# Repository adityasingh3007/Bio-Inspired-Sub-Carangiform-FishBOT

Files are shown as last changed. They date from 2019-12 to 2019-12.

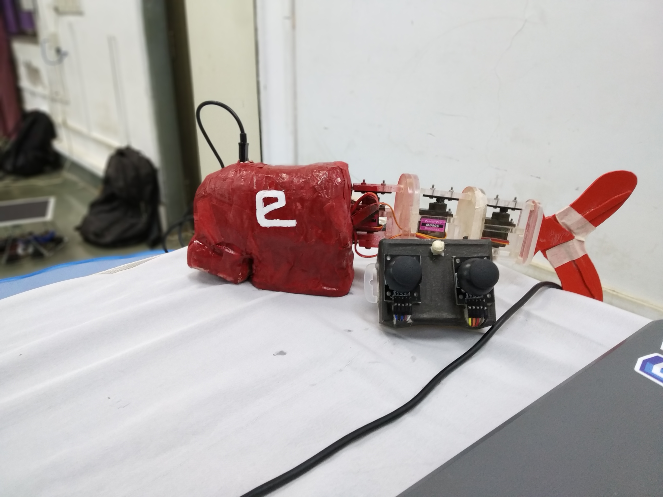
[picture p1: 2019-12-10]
Images/Final_setup.jpg

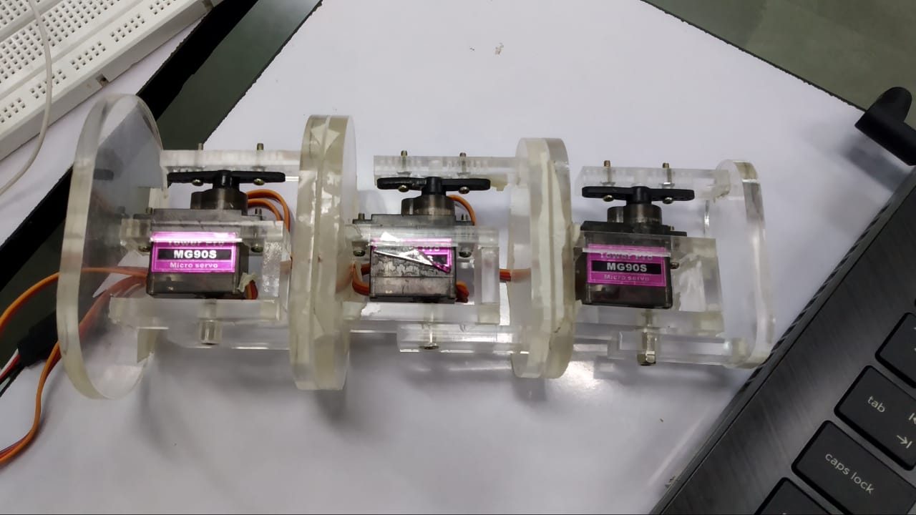
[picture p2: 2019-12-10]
Miscellaneous Files/Extra Images/Assembly_1.jpeg

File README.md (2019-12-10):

# Bio-inspired-sub-carangiform-fishbot-2019

# Abstract:

Researches about underwater propulsion mainly illustrate the use of propellers or thrusters to propel a robot in an underwater environment whereas most of the aquatic animals change their body shape in order to navigate.The shape-change generating propulsion force makes them move forward or backward effectively.The underwater fish robot is a kind of bionic robot which changes its body shape to navigate in underwater environment.The aim of the project is to understand the dynamics of underwater robots in general and the effect of lift, drag and hydrodynamic coefficients on them and to simulate, validate and develop a fish bot robot which is robust enough to carry out underwater exploratory tasks.

## Team:

  • Aditya Kumar Singh [https://github.com/adityasingh3007]

  • Bhavy Shah [https://github.com/Ragnhide]

## Mentors:

  • Rucmenya Bessariya 

  • Saail Narvekar 

  • Lohit Penubaku 

# Repository Organized.

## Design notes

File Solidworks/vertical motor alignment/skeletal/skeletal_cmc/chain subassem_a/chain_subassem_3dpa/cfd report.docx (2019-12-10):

FULL REPORT

System Info

Product | Flow Simulation 2019 SP1.0. Build: 4429
Computer name | DESKTOP-UHNF5GV
User name | Bhavy
Processors | Intel(R) Core(TM) i5-7200U CPU @ 2.50GHz
Memory | 8060 MB / 134217727 MB
Operating system | Windows 10 (or higher) (Version 10.0.17134)
CAD version | SOLIDWORKS 2019 SP1.0
CPU speed | 2701 MHz

General Info

Model | chain assembly_a_3.SLDASM
Project name | Project(1)
Project path | D:\eYSIP\Fishbot\model\F_1\vertical motor alignment\skeletal\skeletal_cmc\chain subassem_a\chain_subassem_3dpa\2
Units system | SI (m-kg-s)
Analysis type | External (not exclude internal spaces)
Exclude cavities without flow conditions | Off
Coordinate system | Global coordinate system
Reference axis | X

INPUT DATA

Global Mesh Settings

Automatic initial mesh: On

Result resolution level: 3

Advanced narrow channel refinement: Off

Refinement in solid region: Off

Geometry Resolution

Evaluation of minimum gap size: Automatic

Evaluation of minimum wall thickness: Automatic

Computational Domain

Size

X min | -0.344 m
X max | 0.482 m
Y min | -0.209 m
Y max | 0.301 m
Z min | -0.189 m
Z max | 0.299 m
X size | 0.826 m
Y size | 0.509 m
Z size | 0.488 m

Boundary Conditions

2D plane flow | None
At X min | Default
At X max | Default
At Y min | Default
At Y max | Default
At Z min | Default
At Z max | Default

Physical Features

Heat conduction in solids: Off

Time dependent: On

Gravitational effects: On

Rotation: Off

Flow type: Laminar only

Cavitation: Off

High Mach number flow: Off

Free surface: Off

Default roughness: 0 micrometer

Gravitational Settings

X component | 0 m/s^2
Y component | -9.81 m/s^2
Z component | 0 m/s^2

Default wall conditions: Adiabatic wall

Ambient Conditions

Thermodynamic parameters | Static Pressure: 5930.00 Pa Temperature: 293.20 K
Velocity parameters | Velocity vector Velocity in X direction: 0.300 m/s Velocity in Y direction: 0 m/s Velocity in Z direction: 0 m/s

Material Settings

Fluids

Water

Fluid Subdomains

Fluid Subdomain 1

Fluids | Water

Faces

Face<20>@ch_t_u-3 Face<3>@ch_t_u-3 Face<165>@9g servo_cmc-3 Face<163>@9g servo_cmc-3 Face<158>@9g servo_cmc-3 Face<148>@9g servo_cmc-3 Face<121>@dual header_cmc-3 Face<110>@dual header_cmc-3 Face<298>@ch_head-1 Face<57>@ch_h_u-3 Face<48>@ch_h_u-3 Face<48>@ch_h_u-2 Face<263>@chain tail_j2_cmc_a-1 Face<261>@chain tail_j2_cmc_a-1 Face<251>@chain tail_j2_cmc_a-1 Face<234>@chain head_j2_cmc_a-1 Face<178>@ch_h_m-2 Face<174>@ch_h_m-2 Face<170>@ch_h_m-2 Face<168>@ch_h_m-2 Face<129>@dual header_cmc-2 Face<128>@dual header_cmc-2 Face<115>@dual header_cmc-2 Face<112>@dual header_cmc-2 Face<109>@dual header_cmc-2 Face<212>@chain tail_cmc_a-1 Face<193>@ch_h_l-2 Face<191>@ch_h_l-2 Face<13>@ch_t_u-1 Face<161>@9g servo_cmc-1 Face<154>@9g servo_cmc-1 Face<112>@dual header_cmc-1 Face<90>@chain head_cmc_a-1 Face<72>@chain tail_j1_cmc_a-1 Face<57>@ch_h_u-1 Face<43>@chain head_j1_cmc_a-1 Face<38>@chain head_j1_cmc_a-1 Face<20>@ch_t_u-2 Face<19>@ch_t_u-2 Face<9>@ch_t_u-2 Face<8>@ch_t_u-2 Face<8>@ch_t_u-3 Face<4>@ch_t_u-3 Face<135>@9g servo_cmc-3 Face<128>@dual header_cmc-3 Face<125>@dual header_cmc-3 Face<124>@dual header_cmc-3 Face<365>@nose_3dpa-1 Face<350>@nose_3dpa-1 Face<337>@nose_3dpa-1 Face<318>@skin_3dpa-1 Face<294>@ch_head-1 Face<274>@ch_head-1 Face<273>@ch_head-1 Face<52>@ch_h_u-2 Face<50>@ch_h_u-2 Face<256>@chain tail_j2_cmc_a-1 Face<222>@chain head_j2_cmc_a-1 Face<218>@chain head_j2_cmc_a-1 Face<133>@dual header_cmc-2 Face<130>@dual header_cmc-2 Face<116>@dual header_cmc-2 Face<200>@chain tail_cmc_a-1 Face<179>@ch_h_m-1 Face<3>@ch_t_u-1 Face<1>@ch_t_u-1 Face<164>@9g servo_cmc-1 Face<89>@chain head_cmc_a-1 Face<78>@chain tail_j1_cmc_a-1 Face<51>@ch_h_u-1 Face<41>@chain head_j1_cmc_a-1 Face<10>@ch_t_u-3 Face<146>@9g servo_cmc-3 Face<235>@ch_t_l-4 Face<336>@nose_3dpa-1 Face<314>@MPU6050-1 Face<302>@lipo_charger_ckt-3 Face<280>@ch_head-1 Face<49>@ch_h_u-3 Face<56>@ch_h_u-2 Face<241>@ch_t_l-2 Face<145>@9g servo_cmc-2 Face<171>@ch_h_m-2 Face<119>@dual header_cmc-2 Face<192>@ch_h_l-3 Face<189>@ch_h_l-3 Face<183>@ch_h_l-3 Face<189>@ch_h_l-1 Face<141>@9g servo_cmc-1 Face<93>@chain head_cmc_a-1 Face<35>@chain head_j1_cmc_a-1 Face<18>@ch_t_u-2 Face<17>@ch_t_u-2 Face<15>@ch_t_u-3 Face<13>@ch_t_u-3 Face<155>@9g servo_cmc-3 Face<149>@9g servo_cmc-3 Face<244>@ch_t_l-3 Face<237>@ch_t_l-3 Face<342>@nose_3dpa-1 Face<330>@skin_3dpa-1 Face<327>@skin_3dpa-1 Face<308>@MPU6050-1 Face<61>@ch_h_u-3 Face<52>@ch_h_u-3 Face<47>@ch_h_u-2 Face<45>@ch_h_u-2 Face<150>@9g servo_cmc-2 Face<127>@dual header_cmc-2 Face<126>@dual header_cmc-2 Face<113>@dual header_cmc-2 Face<211>@chain tail_cmc_a-1 Face<193>@ch_h_l-3 Face<186>@ch_h_l-3 Face<172>@ch_h_m-1 Face<16>@ch_t_u-1 Face<167>@9g servo_cmc-1 Face<150>@9g servo_cmc-1 Face<138>@9g servo_cmc-1 Face<133>@dual header_cmc-1 Face<119>@dual header_cmc-1 Face<100>@chain head_cmc_a-1 Face<98>@chain head_cmc_a-1 Face<77>@chain tail_j1_cmc_a-1 Face<45>@ch_h_u-1 Face<37>@chain head_j1_cmc_a-1 Face<29>@chain head_j1_cmc_a-1 Face<23>@chain head_j1_cmc_a-1 Face<15>@ch_t_u-2 Face<14>@ch_t_u-2 Face<5>@ch_t_u-2 Face<242>@ch_t_l-4 Face<129>@dual header_cmc-3 Face<126>@dual header_cmc-3 Face<333>@skin_3dpa-1 Face<320>@skin_3dpa-1 Face<319>@skin_3dpa-1 Face<269>@lipo-1 Face<279>@ch_head-1 Face<278>@ch_head-1 Face<275>@ch_head-1 Face<270>@lipo-2 Face<54>@ch_h_u-3 Face<50>@ch_h_u-3 Face<57>@ch_h_u-2 Face<265>@chain tail_j2_cmc_a-1 Face<257>@chain tail_j2_cmc_a-1 Face<164>@9g servo_cmc-2 Face<153>@9g servo_cmc-2 Face<151>@9g servo_cmc-2 Face<144>@9g servo_cmc-2 Face<221>@chain head_j2_cmc_a-1 Face<181>@ch_h_m-3 Face<125>@dual header_cmc-2 Face<120>@dual header_cmc-2 Face<197>@chain tail_cmc_a-1 Face<186>@ch_h_l-2 Face<187>@ch_h_l-1 Face<170>@ch_h_m-1 Face<169>@ch_h_m-1 Face<20>@ch_t_u-1 Face<166>@9g servo_cmc-1 Face<146>@9g servo_cmc-1 Face<121>@dual header_cmc-1 Face<81>@chain tail_j1_cmc_a-1 Face<79>@chain tail_j1_cmc_a-1 Face<71>@chain tail_j1_cmc_a-1 Face<47>@ch_h_u-1 Face<22>@ch_t_u-3 Face<7>@ch_t_u-3 Face<161>@9g servo_cmc-3 Face<153>@9g servo_cmc-3 Face<140>@9g servo_cmc-3 Face<241>@ch_t_l-3 Face<239>@ch_t_l-4 Face<369>@buck_cnvrtr-1 Face<368>@buck_cnvrtr-1 Face<118>@dual header_cmc-3 Face<107>@dual header_cmc-3 Face<358>@nose_3dpa-1 Face<353>@nose_3dpa-1 Face<352>@nose_3dpa-1 Face<351>@nose_3dpa-1 Face<297>@ch_head-1 Face<60>@ch_h_u-3 Face<253>@chain tail_j2_cmc_a-1 Face<250>@chain tail_j2_cmc_a-1 Face<248>@chain tail_j2_cmc_a-1 Face<246>@chain tail_j2_cmc_a-1 Face<242>@ch_t_l-2 Face<238>@ch_t_l-2 Face<160>@9g servo_cmc-2 Face<138>@9g servo_cmc-2 Face<178>@ch_h_m-3 Face<180>@ch_h_m-2 Face<131>@dual header_cmc-2 Face<121>@dual header_cmc-2 Face<110>@dual header_cmc-2 Face<191>@ch_h_l-3 Face<196>@ch_h_l-2 Face<177>@ch_h_m-1 Face<174>@ch_h_m-1 Face<9>@ch_t_u-1 Face<8>@ch_t_u-1 Face<159>@9g servo_cmc-1 Face<156>@9g servo_cmc-1 Face<151>@9g servo_cmc-1 Face<124>@dual header_cmc-1 Face<114>@dual header_cmc-1 Face<94>@chain head_cmc_a-1 Face<91>@chain head_cmc_a-1 Face<86>@chain head_cmc_a-1 Face<49>@ch_h_u-1 Face<42>@chain head_j1_cmc_a-1 Face<36>@chain head_j1_cmc_a-1 Face<6>@ch_t_u-2 Face<4>@ch_t_u-2 Face<150>@9g servo_cmc-3 Face<143>@9g servo_cmc-3 Face<139>@9g servo_cmc-3 Face<243>@ch_t_l-4 Face<112>@dual header_cmc-3 Face<109>@dual header_cmc-3 Face<360>@nose_3dpa-1 Face<355>@nose_3dpa-1 Face<349>@nose_3dpa-1 Face<311>@MPU6050-1 Face<284>@ch_head-1 Face<282>@ch_head-1 Face<63>@ch_h_u-3 Face<58>@ch_h_u-3 Face<51>@ch_h_u-3 Face<51>@ch_h_u-2 Face<49>@ch_h_u-2 Face<258>@chain tail_j2_cmc_a-1 Face<154>@9g servo_cmc-2 Face<229>@chain head_j2_cmc_a-1 Face<177>@ch_h_m-3 Face<173>@ch_h_m-3 Face<170>@ch_h_m-3 Face<177>@ch_h_m-2 Face<123>@dual header_cmc-2 Face<107>@dual header_cmc-2 Face<192>@ch_h_l-2 Face<188>@ch_h_l-2 Face<191>@ch_h_l-1 Face<185>@ch_h_l-1 Face<184>@ch_h_l-1 Face<19>@ch_t_u-1 Face<165>@9g servo_cmc-1 Face<118>@dual header_cmc-1 Face<109>@dual header_cmc-1 Face<83>@chain tail_j1_cmc_a-1 Face<74>@chain tail_j1_cmc_a-1 Face<67>@chain tail_j1_cmc_a-1 Face<58>@ch_h_u-1 Face<16>@ch_t_u-3 Face<1>@ch_t_u-3 Face<157>@9g servo_cmc-3 Face<243>@ch_t_l-3 Face<244>@ch_t_l-4 Face<133>@dual header_cmc-3 Face<132>@dual header_cmc-3 Face<122>@dual header_cmc-3 Face<120>@dual header_cmc-3 Face<359>@nose_3dpa-1 Face<356>@nose_3dpa-1 Face<343>@nose_3dpa-1 Face<270>@lipo-1 Face<309>@MPU6050-1 Face<296>@ch_head-1 Face<290>@ch_head-1 Face<283>@ch_head-1 Face<272>@lipo-2 Face<62>@ch_h_u-2 Face<54>@ch_h_u-2 Face<156>@9g servo_cmc-2 Face<141>@9g servo_cmc-2 Face<135>@9g servo_cmc-2 Face<215>@chain head_j2_cmc_a-1 Face<180>@ch_h_m-3 Face<174>@ch_h_m-3 Face<114>@dual header_cmc-2 Face<195>@ch_h_l-3 Face<187>@ch_h_l-2 Face<182>@ch_h_l-2 Face<186>@ch_h_l-1 Face<176>@ch_h_m-1 Face<12>@ch_t_u-1 Face<7>@ch_t_u-1 Face<129>@dual header_cmc-1 Face<127>@dual header_cmc-1 Face<123>@dual header_cmc-1 Face<116>@dual header_cmc-1 Face<97>@chain head_cmc_a-1 Face<87>@chain head_cmc_a-1 Face<31>@chain head_j1_cmc_a-1 Face<6>@ch_t_u-3 Face<138>@9g servo_cmc-3 Face<137>@9g servo_cmc-3 Face<134>@9g servo_cmc-3 Face<240>@ch_t_l-4 Face<236>@ch_t_l-4 Face<370>@buck_cnvrtr-1 Face<366>@buck_cnvrtr-1 Face<127>@dual header_cmc-3 Face<115>@dual header_cmc-3 Face<106>@dual header_cmc-3 Face<340>@nose_3dpa-1 Face<312>@MPU6050-1 Face<306>@MPU6050-1 Face<292>@ch_head-1 Face<53>@ch_h_u-3 Face<63>@ch_h_u-2 Face<59>@ch_h_u-2 Face<252>@chain tail_j2_cmc_a-1 Face<235>@ch_t_l-2 Face<166>@9g servo_cmc-2 Face<157>@9g servo_cmc-2 Face<149>@9g servo_cmc-2 Face<142>@9g servo_cmc-2 Face<217>@chain head_j2_cmc_a-1 Face<171>@ch_h_m-3 Face<175>@ch_h_m-2 Face<122>@dual header_cmc-2 Face<108>@dual header_cmc-2 Face<210>@chain tail_cmc_a-1 Face<199>@chain tail_cmc_a-1 Face<189>@ch_h_l-2 Face<184>@ch_h_l-2 Face<192>@ch_h_l-1 Face<22>@ch_t_u-1 Face<14>@ch_t_u-1 Face<149>@9g servo_cmc-1 Face<143>@9g servo_cmc-1 Face<99>@chain head_cmc_a-1 Face<96>@chain head_cmc_a-1 Face<46>@ch_h_u-1 Face<34>@chain head_j1_cmc_a-1 Face<33>@chain head_j1_cmc_a-1 Face<25>@chain head_j1_cmc_a-1 Face<24>@chain head_j1_cmc_a-1 Face<1>@ch_t_u-2 Face<18>@ch_t_u-3 Face<238>@ch_t_l-4 Face<111>@dual header_cmc-3 Face<332>@skin_3dpa-1 Face<328>@skin_3dpa-1 Face<325>@skin_3dpa-1 Face<315>@skin_3dpa-1 Face<268>@lipo-1 Face<310>@MPU6050-1 Face<277>@ch_head-1 Face<47>@ch_h_u-3 Face<55>@ch_h_u-2 Face<243>@ch_t_l-2 Face<236>@ch_t_l-2 Face<167>@9g servo_cmc-2 Face<136>@9g servo_cmc-2 Face<134>@9g servo_cmc-2 Face<233>@chain head_j2_cmc_a-1 Face<172>@ch_h_m-2 Face<207>@chain tail_cmc_a-1 Face<184>@ch_h_l-3 Face<182>@ch_h_l-3 Face<196>@ch_h_l-1 Face<182>@ch_h_l-1 Face<171>@ch_h_m-1 Face<21>@ch_t_u-1 Face<160>@9g servo_cmc-1 Face<92>@chain head_cmc_a-1 Face<70>@chain tail_j1_cmc_a-1 Face<62>@ch_h_u-1 Face<52>@ch_h_u-1 Face<26>@chain head_j1_cmc_a-1 Face<22>@ch_t_u-2 Face<21>@ch_t_u-2 Face<13>@ch_t_u-2 Face<2>@ch_t_u-3 Face<162>@9g servo_cmc-3 Face<159>@9g servo_cmc-3 Face<144>@9g servo_cmc-3 Face<245>@ch_t_l-3 Face<241>@ch_t_l-4 Face<364>@nose_3dpa-1 Face<354>@nose_3dpa-1 Face<344>@nose_3dpa-1 Face<329>@skin_3dpa-1 Face<326>@skin_3dpa-1 Face<272>@lipo-1 Face<271>@lipo-1 Face<305>@MPU6050-1 Face<56>@ch_h_u-3 Face<58>@ch_h_u-2 Face<262>@chain tail_j2_cmc_a-1 Face<259>@chain tail_j2_cmc_a-1 Face<254>@chain tail_j2_cmc_a-1 Face<240>@ch_t_l-2 Face<223>@chain head_j2_cmc_a-1 Face<111>@dual header_cmc-2 Face<194>@ch_h_l-2 Face<185>@ch_h_l-2 Face<195>@ch_h_l-1 Face<188>@ch_h_l-1 Face<183>@ch_h_l-1 Face<175>@ch_h_m-1 Face<15>@ch_t_u-1 Face<153>@9g servo_cmc-1 Face<148>@9g servo_cmc-1 Face<147>@9g servo_cmc-1 Face<144>@9g servo_cmc-1 Face<139>@9g servo_cmc-1 Face<130>@dual header_cmc-1 Face<125>@dual header_cmc-1 Face<88>@chain head_cmc_a-1 Face<40>@chain head_j1_cmc_a-1 Face<12>@ch_t_u-2 Face<11>@ch_t_u-2 Face<160>@9g servo_cmc-3 Face<141>@9g servo_cmc-3 Face<239>@ch_t_l-3 Face<245>@ch_t_l-4 Face<362>@nose_3dpa-1 Face<335>@nose_3dpa-1 Face<291>@ch_head-1 Face<287>@ch_head-1 Face<286>@ch_head-1 Face<271>@lipo-2 Face<268>@lipo-2 Face<45>@ch_h_u-3 Face<53>@ch_h_u-2 Face<158>@9g servo_cmc-2 Face<155>@9g servo_cmc-2 Face<152>@9g servo_cmc-2 Face<231>@chain head_j2_cmc_a-1 Face<225>@chain head_j2_cmc_a-1 Face<224>@chain head_j2_cmc_a-1 Face<220>@chain head_j2_cmc_a-1 Face<169>@ch_h_m-3 Face<173>@ch_h_m-2 Face<132>@dual header_cmc-2 Face<213>@chain tail_cmc_a-1 Face<205>@chain tail_cmc_a-1 Face<195>@ch_h_l-2 Face<183>@ch_h_l-2 Face<194>@ch_h_l-1 Face<178>@ch_h_m-1 Face<4>@ch_t_u-1 Face<155>@9g servo_cmc-1 Face<122>@dual header_cmc-1 Face<113>@dual header_cmc-1 Face<101>@chain head_cmc_a-1 Face<65>@chain tail_j1_cmc_a-1 Face<27>@chain head_j1_cmc_a-1 Face<10>@ch_t_u-2 Face<7>@ch_t_u-2 Face<21>@ch_t_u-3 Face<167>@9g servo_cmc-3 Face<166>@9g servo_cmc-3 Face<156>@9g servo_cmc-3 Face<152>@9g servo_cmc-3 Face<113>@dual header_cmc-3 Face<361>@nose_3dpa-1 Face<345>@nose_3dpa-1 Face<322>@skin_3dpa-1 Face<317>@skin_3dpa-1 Face<313>@MPU6050-1 Face<303>@lipo_charger_ckt-3 Face<301>@lipo_charger_ckt-3 Face<300>@lipo_charger_ckt-3 Face<299>@lipo_charger_ckt-3 Face<295>@ch_head-1 Face<288>@ch_head-1 Face<281>@ch_head-1 Face<276>@ch_head-1 Face<55>@ch_h_u-3 Face<44>@ch_h_u-3 Face<61>@ch_h_u-2 Face<44>@ch_h_u-2 Face<264>@chain tail_j2_cmc_a-1 Face<162>@9g servo_cmc-2 Face<147>@9g servo_cmc-2 Face<140>@9g servo_cmc-2 Face<228>@chain head_j2_cmc_a-1 Face<169>@ch_h_m-2 Face<204>@chain tail_cmc_a-1 Face<203>@chain tail_cmc_a-1 Face<198>@chain tail_cmc_a-1 Face<194>@ch_h_l-3 Face<190>@ch_h_l-3 Face<18>@ch_t_u-1 Face<10>@ch_t_u-1 Face<2>@ch_t_u-1 Face<158>@9g servo_cmc-1 Face<152>@9g servo_cmc-1 Face<140>@9g servo_cmc-1 Face<135>@9g servo_cmc-1 Face<120>@dual header_cmc-1 Face<115>@dual header_cmc-1 Face<111>@dual header_cmc-1 Face<107>@dual header_cmc-1 Face<80>@chain tail_j1_cmc_a-1 Face<73>@chain tail_j1_cmc_a-1 Face<68>@chain tail_j1_cmc_a-1 Face<60>@ch_h_u-1 Face<59>@ch_h_u-1 Face<39>@chain head_j1_cmc_a-1 Face<16>@ch_t_u-2 Face<3>@ch_t_u-2 Face<14>@ch_t_u-3 Face<5>@ch_t_u-3 Face<147>@9g servo_cmc-3 Face<145>@9g servo_cmc-3 Face<242>@ch_t_l-3 Face<237>@ch_t_l-4 Face<131>@dual header_cmc-3 Face<119>@dual header_cmc-3 Face<117>@dual header_cmc-3 Face<116>@dual header_cmc-3 Face<346>@nose_3dpa-1 Face<341>@nose_3dpa-1 Face<339>@nose_3dpa-1 Face<334>@nose_3dpa-1 Face<324>@skin_3dpa-1 Face<316>@skin_3dpa-1 Face<293>@ch_head-1 Face<285>@ch_head-1 Face<267>@lipo-2 Face<46>@ch_h_u-3 Face<46>@ch_h_u-2 Face<161>@9g servo_cmc-2 Face<146>@9g servo_cmc-2 Face<143>@9g servo_cmc-2 Face<139>@9g servo_cmc-2 Face<230>@chain head_j2_cmc_a-1 Face<226>@chain head_j2_cmc_a-1 Face<117>@dual header_cmc-2 Face<106>@dual header_cmc-2 Face<209>@chain tail_cmc_a-1 Face<185>@ch_h_l-3 Face<190>@ch_h_l-2 Face<193>@ch_h_l-1 Face<190>@ch_h_l-1 Face<137>@9g servo_cmc-1 Face<136>@9g servo_cmc-1 Face<131>@dual header_cmc-1 Face<105>@chain head_cmc_a-1 Face<104>@chain head_cmc_a-1 Face<103>@chain head_cmc_a-1 Face<84>@chain tail_j1_cmc_a-1 Face<61>@ch_h_u-1 Face<50>@ch_h_u-1 Face<28>@chain head_j1_cmc_a-1 Face<12>@ch_t_u-3 Face<9>@ch_t_u-3 Face<142>@9g servo_cmc-3 Face<236>@ch_t_l-3 Face<235>@ch_t_l-3 Face<371>@buck_cnvrtr-1 Face<363>@nose_3dpa-1 Face<62>@ch_h_u-3 Face<266>@chain tail_j2_cmc_a-1 Face<249>@chain tail_j2_cmc_a-1 Face<237>@ch_t_l-2 Face<165>@9g servo_cmc-2 Face<159>@9g servo_cmc-2 Face<219>@chain head_j2_cmc_a-1 Face<214>@chain head_j2_cmc_a-1 Face<179>@ch_h_m-3 Face<176>@ch_h_m-3 Face<175>@ch_h_m-3 Face<168>@ch_h_m-3 Face<196>@ch_h_l-3 Face<187>@ch_h_l-3 Face<180>@ch_h_m-1 Face<168>@ch_h_m-1 Face<17>@ch_t_u-1 Face<162>@9g servo_cmc-1 Face<157>@9g servo_cmc-1 Face<134>@9g servo_cmc-1 Face<132>@dual header_cmc-1 Face<126>@dual header_cmc-1 Face<108>@dual header_cmc-1 Face<82>@chain tail_j1_cmc_a-1 Face<76>@chain tail_j1_cmc_a-1 Face<75>@chain tail_j1_cmc_a-1 Face<64>@chain tail_j1_cmc_a-1 Face<63>@ch_h_u-1 Face<30>@chain head_j1_cmc_a-1 Face<19>@ch_t_u-3 Face<164>@9g servo_cmc-3 Face<151>@9g servo_cmc-3 Face<136>@9g servo_cmc-3 Face<238>@ch_t_l-3 Face<367>@buck_cnvrtr-1 Face<108>@dual header_cmc-3 Face<347>@nose_3dpa-1 Face<338>@nose_3dpa-1 Face<323>@skin_3dpa-1 Face<267>@lipo-1 Face<307>@MPU6050-1 Face<304>@lipo_charger_ckt-3 Face<60>@ch_h_u-2 Face<255>@chain tail_j2_cmc_a-1 Face<247>@chain tail_j2_cmc_a-1 Face<245>@ch_t_l-2 Face<163>@9g servo_cmc-2 Face<148>@9g servo_cmc-2 Face<232>@chain head_j2_cmc_a-1 Face<181>@ch_h_m-2 Face<176>@ch_h_m-2 Face<118>@dual header_cmc-2 Face<206>@chain tail_cmc_a-1 Face<202>@chain tail_cmc_a-1 Face<181>@ch_h_m-1 Face<6>@ch_t_u-1 Face<5>@ch_t_u-1 Face<163>@9g servo_cmc-1 Face<102>@chain head_cmc_a-1 Face<95>@chain head_cmc_a-1 Face<56>@ch_h_u-1 Face<53>@ch_h_u-1 Face<48>@ch_h_u-1 Face<17>@ch_t_u-3 Face<11>@ch_t_u-3 Face<154>@9g servo_cmc-3 Face<240>@ch_t_l-3 Face<130>@dual header_cmc-3 Face<123>@dual header_cmc-3 Face<114>@dual header_cmc-3 Face<357>@nose_3dpa-1 Face<348>@nose_3dpa-1 Face<331>@skin_3dpa-1 Face<321>@skin_3dpa-1 Face<289>@ch_head-1 Face<269>@lipo-2 Face<59>@ch_h_u-3 Face<260>@chain tail_j2_cmc_a-1 Face<244>@ch_t_l-2 Face<239>@ch_t_l-2 Face<137>@9g servo_cmc-2 Face<227>@chain head_j2_cmc_a-1 Face<216>@chain head_j2_cmc_a-1 Face<172>@ch_h_m-3 Face<179>@ch_h_m-2 Face<124>@dual header_cmc-2 Face<208>@chain tail_cmc_a-1 Face<201>@chain tail_cmc_a-1 Face<188>@ch_h_l-3 Face<173>@ch_h_m-1 Face<11>@ch_t_u-1 Face<145>@9g servo_cmc-1 Face<142>@9g servo_cmc-1 Face<128>@dual header_cmc-1 Face<117>@dual header_cmc-1 Face<110>@dual header_cmc-1 Face<106>@dual header_cmc-1 Face<85>@chain head_cmc_a-1 Face<69>@chain tail_j1_cmc_a-1 Face<66>@chain tail_j1_cmc_a-1 Face<55>@ch_h_u-1 Face<54>@ch_h_u-1 Face<44>@ch_h_u-1 Face<32>@chain head_j1_cmc_a-1 Face<2>@ch_t_u-2
Coordinate system | Global coordinate system
Reference axis | X
Thermodynamic Parameters | Static Pressure: 5930.00 Pa Pressure potential: On Temperature: 293.20 K
Velocity Parameters | Velocity in X direction: 0.300 m/s Velocity in Y direction: 0 m/s Velocity in Z direction: 0 m/s
Flow type | Laminar Only
Cavitation | Off
Refer to the origin | Off

Boundary Conditions

Real Wall 1

Type | Real wall
Faces
Coordinate system | Global coordinate system
Reference axis | X

Goals

Global Goals

GG Minimum Static Pressure 1

Type | Global Goal
Goal type | Static Pressure
Calculate | Minimum value
Coordinate system | Global coordinate system
Use in convergence | On

GG Average Total Pressure 1

Type | Global Goal
Goal type | Total Pressure
Calculate | Average value
Coordinate system | Global coordinate system
Use in convergence | On

GG Maximum Dynamic Pressure 1

Type | Global Goal
Goal type | Dynamic Pressure
Calculate | Maximum value
Coordinate system | Global coordinate system
Use in convergence | On

GG Minimum Velocity (X) 1

Type | Global Goal
Goal type | Velocity (X)
Calculate | Minimum value
Coordinate system | Global coordinate system
Use in convergence | On

Calculation Control Options

Finish Conditions

Finish Conditions | If one is satisfied
Maximum physical time | 1.000 s

Solver Refinement

Refinement: Disabled

Results Saving

Save before refinement | On

Advanced Control Options

Flow Freezing

Flow freezing strategy | Disabled

Manual time step (Freezing): Off

Manual time step: Off

RESULTS

Document1 Page 1 of 1 18.06.2019

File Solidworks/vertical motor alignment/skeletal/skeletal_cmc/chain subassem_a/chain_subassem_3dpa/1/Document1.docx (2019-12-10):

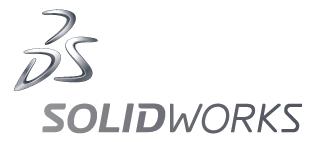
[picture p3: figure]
Description: Description: sw_vert_gray_short

[Company logo here]
[company name here] | [city, state here] | [company url here] | Fluid Flow Simulation Project Report

[name] ∙ | [title] | ∙ ∙ [email address] ∙ | (###) ###-####

# SOLIDWORKS Flow Simulation

# Project Report

March 26, 2014

[Model Picture here]

Learn more about SOLIDWORKS Flow Simulation (https://www.solidworks.com/sw/products/simulation/flow-simulation.htm)

# Table of Contents

# 1 General Information

Objective of the simulation: Lorem ipsum dolor sit amet, consectetur adipiscing elit. Ut a pulvinar lacus. Vivamus adipiscing adipiscing eleifend. Pellentesque eget ante in ante suscipit gravida in non lorem. Suspendisse hendrerit sagittis lacus non aliquam. Proin pellentesque, lorem quis consequat porta, lectus nunc vestibulum lectus, nec rhoncus libero dui ut felis. Vestibulum eu aliquet tellus. Curabitur suscipit ornare sem. Suspendisse pulvinar pharetra ultrices. Suspendisse a quam massa

## 1.1 Analysis Environment

Software Product: Flow Simulation 2019 SP1.0. Build: 4429

CPU Type: Intel(R) Core(TM) i5-7200U CPU @ 2.50GHz

CPU Speed: 2701 (400) MHz

RAM: 8060 MB / 134217727 MB

Operating System: Windows 10 (or higher) (Version 10.0.17134)

## 1.2 Model Information

Model Name: chain assembly_a_3.SLDASM

Project Name: Project(1)

## 1.3 Project Comments:

Unit System: SI (m-kg-s)

Analysis Type: External (not exclude internal spaces)

## 1.4 Size of Computational Domain

Size

X min | -0.344 m
X max | 0.482 m
Y min | -0.209 m
Y max | 0.301 m
Z min | -0.189 m
Z max | 0.299 m
X size | 0.826 m
Y size | 0.509 m
Z size | 0.488 m

## 1.5 Simulation Parameters

### 1.5.1 Mesh Settings

#### 1.5.1.1 Basic Mesh

#### 1.5.1.2 Analysis Mesh

Total Cell count:

Fluid Cells:

Solid Cells:

Partial Cells:

Trimmed Cells:

#### 1.5.1.3 Additional Physical Calculation Options

Heat Transfer Analysis: Heat conduction in solids: Off

Flow Type: Laminar only

Time-Dependent Analysis: On

Gravity: On

Radiation:

Humidity:

Default Wall Roughness: 0 micrometer

### 1.5.2 Material Settings

Material Settings

Fluids

Water

### 1.5.3 Initial Conditions

Ambient Conditions

Thermodynamic parameters | Static Pressure: 5930.00 Pa Temperature: 298.00 K
Velocity parameters | Velocity vector Velocity in X direction: 0.250 m/s Velocity in Y direction: 0 m/s Velocity in Z direction: 0 m/s

### 1.5.4 Boundary Conditions

Boundary Conditions

Real Wall 1

Type | Real wall
Faces | skin_3dpa-1/Shell1//Face skin_3dpa-1/Shell1//Face nose_3dpa-1/Sweep1//Face skin_3dpa-1/Shell1//Face skin_3dpa-1/Shell1//Face skin_3dpa-1/Shell1//Face skin_3dpa-1/Shell1//Face ch_head-1/Cut-Sweep1//Face skin_3dpa-1/Shell1//Face nose_3dpa-1/Sweep1//Face
Coordinate system | Global coordinate system
Reference axis | X

### 1.5.5 Volumetric Heat Sources

### 1.5.6 Engineering Goals

## 1.6 Analysis Time

Calculation Time: 0 s

Number of Iterations: 0

Warnings:

# 3 Results

## 3.1 Analysis Goals

## 3.2 Global Min-Max-Table

## 3.3 Results

## 3.4 Conclusion

Lorem ipsum dolor sit amet, consectetur adipiscing elit. Ut a pulvinar lacus. Vivamus adipiscing adipiscing eleifend. Pellentesque eget ante in ante suscipit gravida in non lorem. Suspendisse hendrerit sagittis lacus non aliquam. Proin pellentesque, lorem quis consequat porta, lectus nunc vestibulum lectus, nec rhoncus libero dui ut felis. Vestibulum eu aliquet tellus. Curabitur suscipit ornare sem. Suspendisse pulvinar pharetra ultrices. Suspendisse a quam massa

# 5 Appendix

## 5.1 Material Data

Engineering Database

Liquids

Water

Path: Liquids Pre-Defined

Density

Dynamic viscosity

Specific heat (Cp)

Thermal conductivity

Cavitation effect: Yes

Temperature: 0 K

Saturation pressure: 0 Pa

Radiation properties: No

Fluid Flow Simulation Report

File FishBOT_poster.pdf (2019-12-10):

# Bio-Inspired Sub-carangiform Fishbot

## Aditya Kumar Singh, Bhavy Shah, Mentor: Rucmenya, Lohit, Saail

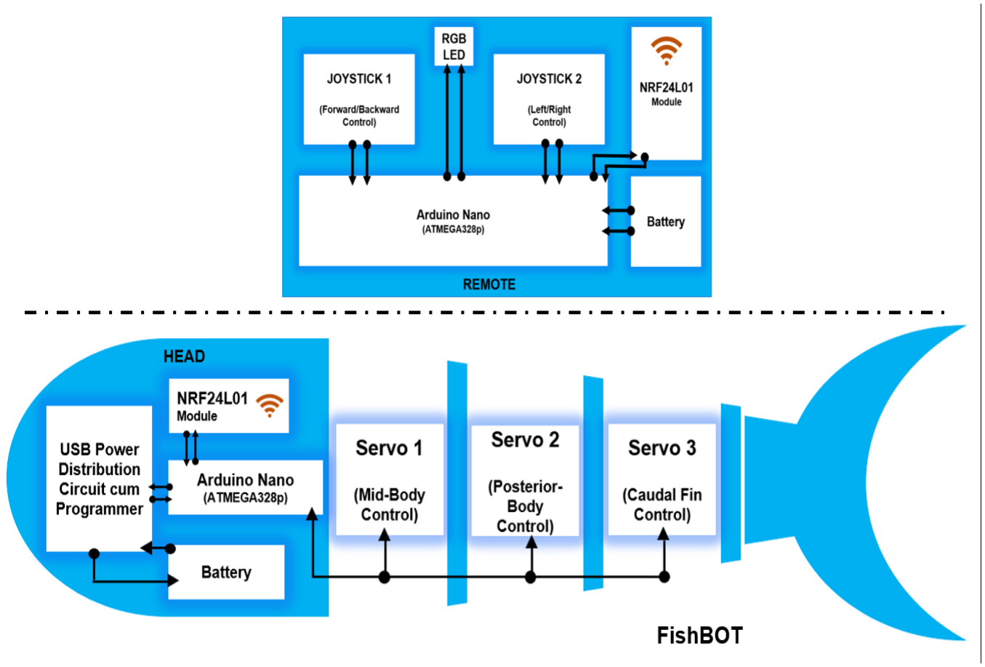
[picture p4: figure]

## e-Yantra Summer Internship Project 2019

## Abstract

Underwater robotics is a great option to carry out various underwater operations like environmental inspection, monitoring natural resources, defense operations, underwater machinery inspection and many more, remotely.

## Objective

The objective of this project is to design, develop & build a bionic subcarangiform fish that can swim and can be controlled remotely.

## Introduction

Nature has always remained an inspiration to

build and innovate robots that operates similar to

real-world beings. A fish has got typical smooth

motion when it comes to underwater navigation.

It uses undulated body motion and caudal fin to

move forward and pectoral & pelvic fins for

turning operations. This robo-fish has geometry

and body resembling to a subcarangiform fish.

Block Diagram | Solidworks CAD model

## Features

+ Imitates swimming pattern of a subcarangiform fish and has streamline design.
+ Multi-segmented body for a sinusoidal motion of the body. (Length is 36cm and Turning Radius is 18cm).
+ Manevuring of the fish is achieved using only Caudal Fin and the Body motion.
+ Wirelessly controlled using NRF24L01 module (2.4 GHz ISM Band) through SPI protocol.
+ Waterproofing of electronics using plasticizer resin.

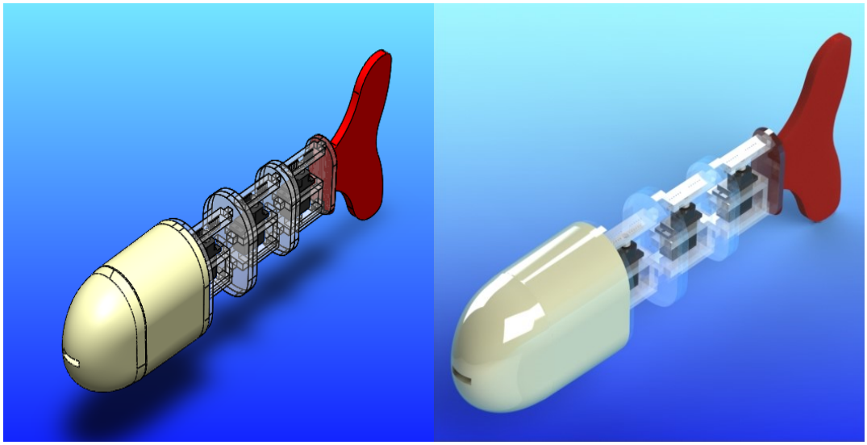
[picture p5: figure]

## Actual Model

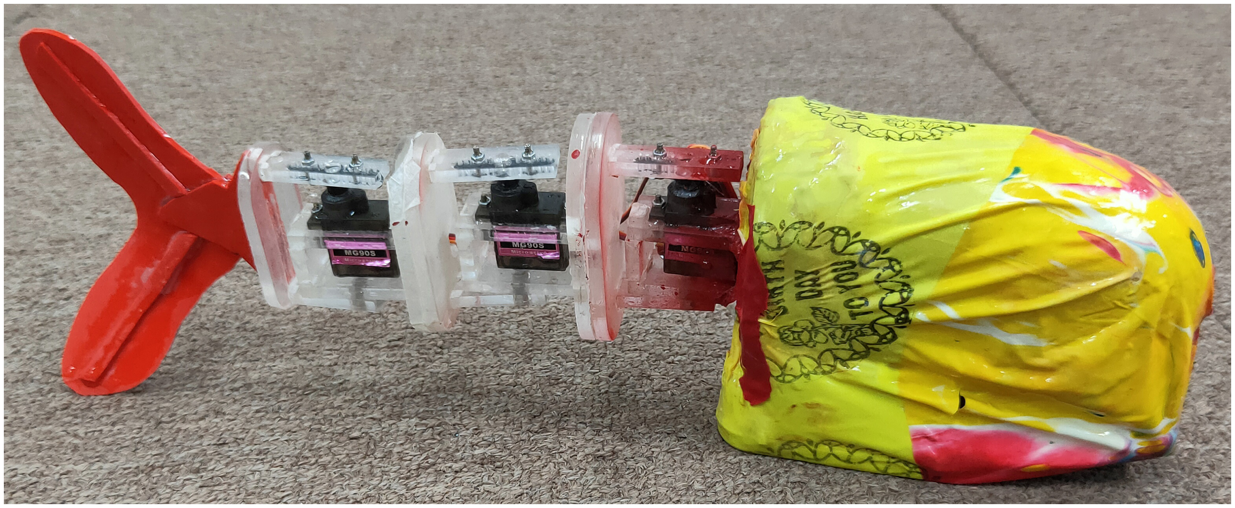
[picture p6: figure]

## Application

+ Underwater survillance.
+ Underwater exploration.
+ Robot-animal interaction.
+ Aquatic Environmental monitoring. + Education and outreach.

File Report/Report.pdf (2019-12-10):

## e-YSIP 2019

### Bio-Inspired Sub-carangiform

## FishBOT

### Intern 1: Aditya Kumar Singh Intern 2: Bhavy Shah Mentor Name: Rucmenya Bessariya Lohit Penubaku Saail Narvekar Duration of Internship: 22/05/2019 − 05/07/2019

2019, e-Yantra Publication

# Bio-Inspired Sub-carangiform Fish-BOT

## Abstract

Nature has always worked as an inspirational source for the robotics world to create & innovate things in order to understand and imitate it. This project on the same basis, is all about how to design & imitate a subcarangiform fish in respect to the nature’s creation. The FishBOT has got a 3 joint body locomotion controlled using micro servos. The caudal fin is used to generate the force vortex for each forward push and also the turns are controlled only by using lateral shift of body & caudal fin.

### Completion status

Working prototype which can swim underwater has been accomplished with great speed and efficiency as well as turning on both side can be done with effective turning radius ranging 15 to 30 cm. The length of the bot is 36 cm. Also, it is controlled using remote by NRF24L01 transceiver module. It has a battery backup of 30 minutes.

## 1.1 Hardware parts

- Arduino Nano (with Cable) (2 Pcs), Datasheet, page 1, Vendor link (https://www.amazon.in/SunRobotics-Arduino-Nano-USB-Cable/dp/B072VQL7WJ)
- NRF24L01 Module (2 Pcs), Datasheet, page 1, Vendor link (https://www.amazon.in/REES52-NRF24L01-Wireless-Transceiver-Arduino/dp/0070923507)
- Lipo Battery, 3.7 Volts (4 Pcs), Vendor link (https://www.amazon.in/Invento-battery-40x35x5mm-Quadcopter-Helicopter/dp/B07GL3VT81?s=gateway)
- Micro Servo Motor (3 Pcs), Datasheet, page 1, Vendor link (https://www.amazon.in/Robodo-Electronics-Tower-Micro-Servo/dp/B00MTFFAE0)
- LM323T Voltage Regulator (1 Pc), Datasheet, page 1, Vendor link (https://www.amazon.co.uk/LM323T-terminal-positive-regulator-220-casing/dp/B0747TDDCC)

1

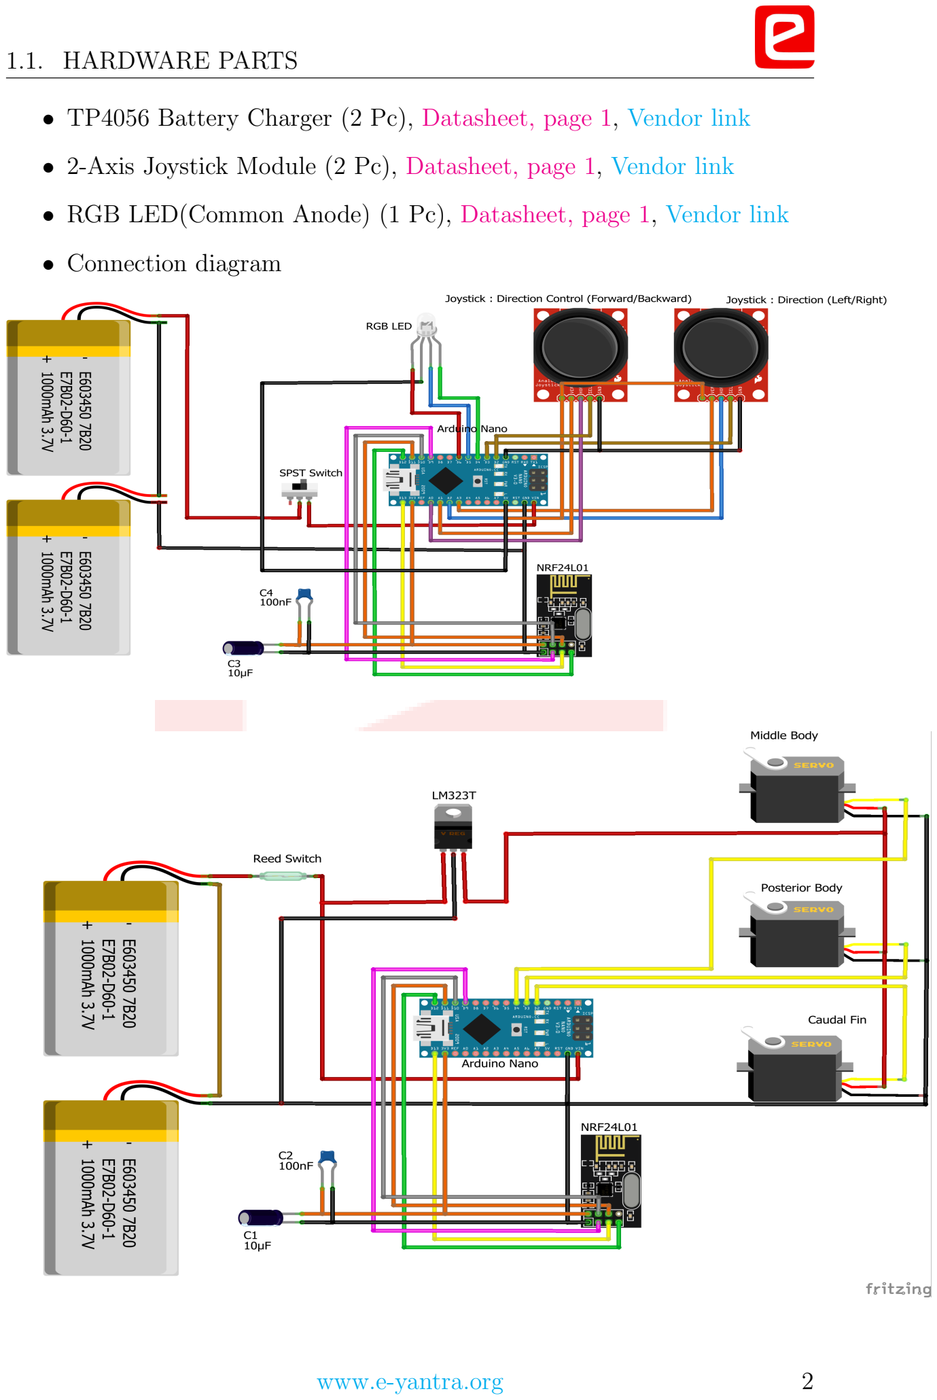
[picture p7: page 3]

1.1. HARDWARE PARTS
- TP4056 Battery Charger (2 Pc), Datasheet, page 1, Vendor link (https://robu.in/product/tp4056-1a-lipo-battery-charging-board-micro-usb-with-current-protection/)
- 2-Axis Joystick Module (2 Pc), Datasheet, page 1, Vendor link (https://www.amazon.in/Dual-Axis-Joystick-Module-Arduino-Devices/dp/B00WFDJS26)
- RGB LED(Common Anode) (1 Pc), Datasheet, page 1, Vendor link (https://www.amazon.in/Generic-PZIN14016715-Anode-Color-Diffused/dp/B01EE3NJJC?s=gateway)
- Connection diagram
www.e-yantra.org | 2

1.2. SOFTWARE USED

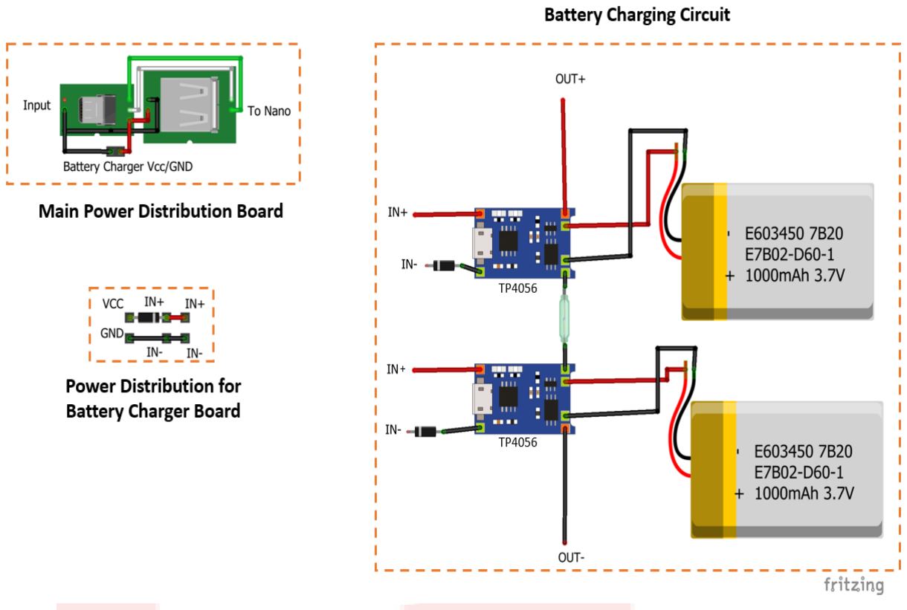
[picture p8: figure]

## 1.2 Software used

- Arduino IDE, Version:1.8.5, Link (https://www.arduino.cc/en/Main/OldSoftwareReleases)
- Solidworks Version: 2019, Link (https://my.solidworks.com/try-solidworks)
- Installation steps:

– Arduino IDE : Installation Guide (https://www.arduino.cc/en/Guide/Windows)

– Solidworks : Installation Guide (https://www.solidworks.com/sw/education/student-installation-guides-and-support.htm)

## 1.3 Assembly of Mechanical design & Electronics hardware

Getting Mechanical design model.

Get the Solidworks design of parts and assembly from this link: Link

www.e-yantra.org | 3

1.3. ASSEMBLY OF MECHANICAL DESIGN & ELECTRONICS HARDWARE

### Getting mechanical parts

Get the acrylic parts laser cut and the head & nose portion of the fish 3D printed.

### Waterproofing servo motors

- Unscrew the servos from the bottom. On the circuitry parts apply 2-3 coatings of plasticizer resin.
- On the top gear part, apply hydrophobic grease and then screw it back.
- Further, apply multiple coatings of the resin on entire servo motor body (keeping care near the shaft part) and let it dry.
- Before fitting the servo motor on the assembly, just test it once for underwater conditions.

### Assembling the skeleton body

- Assemble the skeletal part joint wise and also place the motors in each joint. Assemble each joint to get the complete body.
- For joining the parts, any adhesive which glues together acrylics can be used.
- Be careful while joining, all the parts attached to the main hub should be 90 deg. This is to ensure that the chain has minimal deformation.
- Finally you should have something like this:-

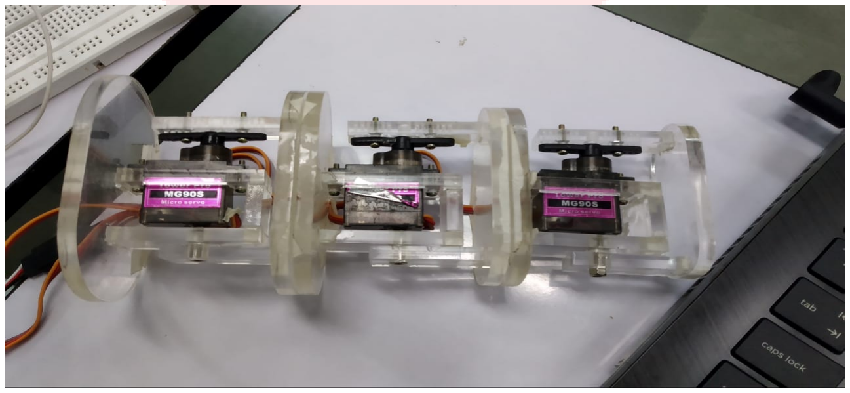
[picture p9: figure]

www.e-yantra.org | 4

1.3. ASSEMBLY OF MECHANICAL DESIGN & ELECTRONICS HARDWARE

### Waterproof Electronics

- Similar to motors, waterproof all electronics components using plasticizer resin. Make sure to apply 2-3 coatings.
- Waterproof the electronics only when they are placed on their position in final PCB. Avoid applying coating on the pins of the microcontrollers or other circuits.

### Circuit assembly

- Assemble the circuit as per the given circuit diagram in section 1.1.
- The circuit can be designed on perfboard. This you have to do it on your own. There is no footprints for this.
- Finally test the circuit once before fitting it in its actual position.

### Electronics in fish

- After successful testing, place the electronics in fish body as per suitable positions.
- Look for the wire lengths of servos motor carefully. Dont’t restrict the servo movements because of the wires.
- Before sealing, test the whole setup again. From reeed switch to communication between remote and BOT everything.

### Assembling the head body

- Now, assemble the head & nose using silicon and also cover the whole body with plasticizer and then coat with epoxy for water proofing.
- Test for the waterproofing of the BOT completely before actually deploying it in pool.
www.e-yantra.org | 5

1.4. SOFTWARE AND CODE

## 1.4 Software and Code

Github link (https://github.com/eyantra-eysip/Bio-inspired-sub-carangiform-fishbot-2019) for the repository of code
Brief explanation of various parts of code:
- NRF Communication:
1. For maximum distance, power is kept maximum.
2. Data transfer speed is set to 250Kbps.
3. Auto acknowledge is enabled.
4. Remote send ’F’, ’B’, ’L’, ’R’ to BOT and the BOT receives it along with speed ranging from 0-4. For handshaking the BOT sends back numbers to tell that data was received successfully.
- Fish’s Motion:
1. The fish’s motion is inspired from one of the famous undulatory motion - ”Serpentine Motion”.
2. More information about the motion can be obtained here:- Link (https://www.instructables.com/id/Snake-Robot-1/)
3. For turning along with the parameters, the first link can be fixed to its respective turn side and rest all links can be moved.
- Remote:
1. The remote uses handshaking technique to communicate with the BOT.
2. The commands used can be found in the code itself. Along with direction, speed is also sent in form of numbers ranging from 0-4.
3. The more the joysticks are bent, the more will be speed. This is done via mapping the ADC values from the joystick to 0-5 using map() function.
www.e-yantra.org | 6

1.5. USE AND DEMO

## 1.5 Use and Demo

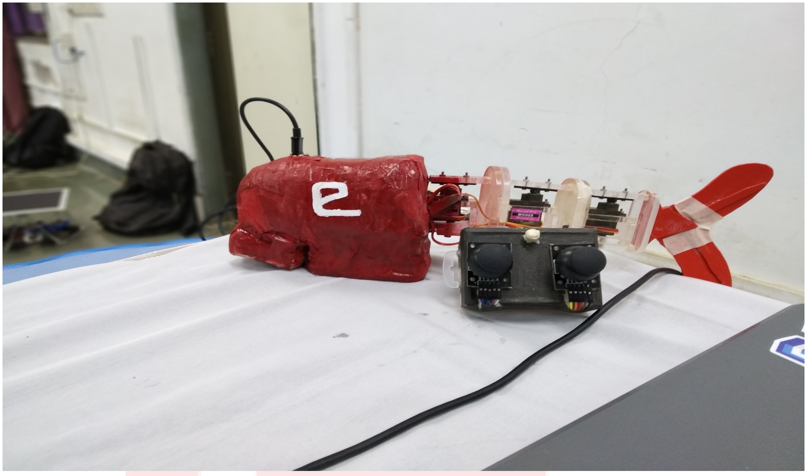
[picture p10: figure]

### Usage Instructions:

- Handle with care or it may cause water-proofing issues.
- Do note that the magnetic-switch is off while charging batteries or data transfer.
- Do not sink completely in water.
- If at any time during operation, bubbles start coming out of the BOT, immediately take it out from the water.
- While plugging in for charging or data transfer, make sure that the USB port is not wet.

Youtube Link (https://youtu.be/v-eBw23lZjE) of demonstration video

www.e-yantra.org | 7

1.6. FUTURE WORK

## 1.6 Future Work

- More efficient control of buoyancy can be resulted into variable depth swims.
- Size of the fish can be reduced by optimizing mechanical design and also using smaller electronics.
- It can be made in autonomous working style.
- Design can be made more imitating by implementation of subsidiary fins.
- More features can be added as per requirement.

## 1.7 Bug report and Challenges

- Size of the fishbot increases considerably on implementing regular size components.
- Water-proof mechanical design is hard to obtain with sufficient repellency to water.
- Electronics water-proofing to a certain perfection was challenging.
- Maintaining the body buoyancy so that fish remains stable while its motion is a challenging task to accomplish.
- Providing proper occupancy to all components with getting them to work efficiently as well as maintaining minimum size.
www.e-yantra.org | 8

# Bibliography

[1] Larry Hardesty, Soft robotic fish moves like the real thing, 2014
[2] Huosheng Hu, Biologically inspired design of Autonomous robotic fish at Essex, 2006
[3] AIRO, The MIRO maker, MIRO: The only biomimetic robotic fish in the world, 2018
[4] Jaywant H Arakeri, Fluid Mechanics of Fish Swimming, 1997
[5] computerphile, | Robotic | fish | - | computerphile | https:// youtu.be/
F1tS-qGCE0U (https://youtu.be/F1tS-qGCE0U) , 2019
[6] Eric Dirgahayu, RoboFish made from PVC water pipe, 2015
[7] Junzhi Yu, Shifeng Chen, Zhengxing Wu, Weibing Wang, On a Miniature free-swimming Robotic fish with multiple sensors, 2017
[8] Joseph DelPreto, Daniela Rus, Sofi- The soft robotic fish, 2014

9

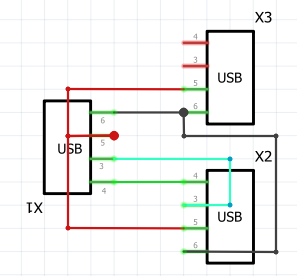
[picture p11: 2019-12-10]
Miscellaneous Files/Electronics/Circuit/USB_2.PNG

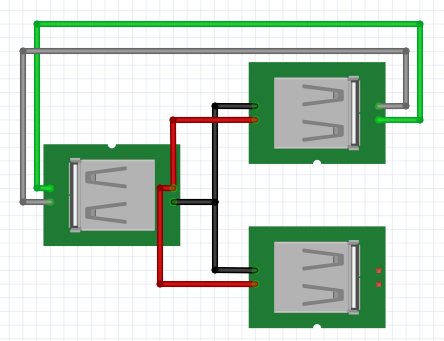
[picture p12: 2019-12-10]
Miscellaneous Files/Electronics/Circuit/USB_1.PNG

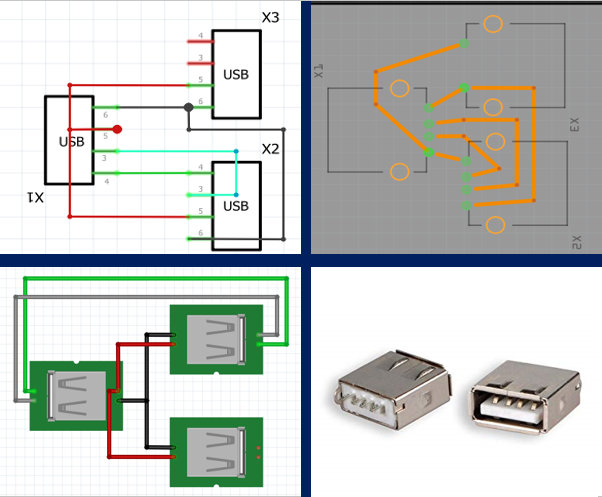
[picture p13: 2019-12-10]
Miscellaneous Files/Electronics/Circuit/USB_Connection.PNG

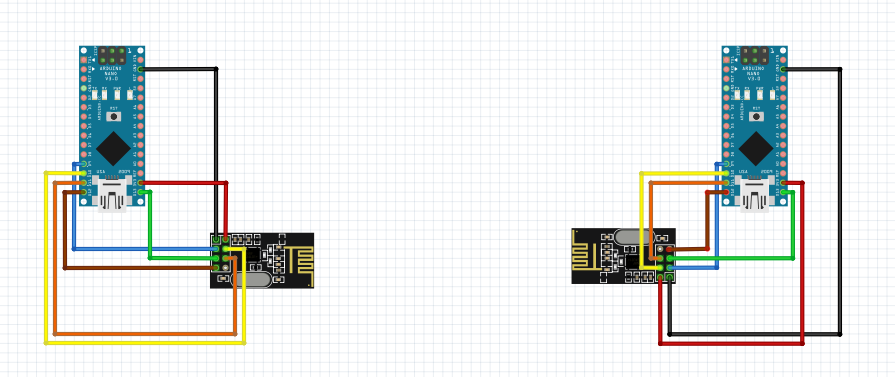
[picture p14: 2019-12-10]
Miscellaneous Files/Electronics/Circuit/NRF24L01.png

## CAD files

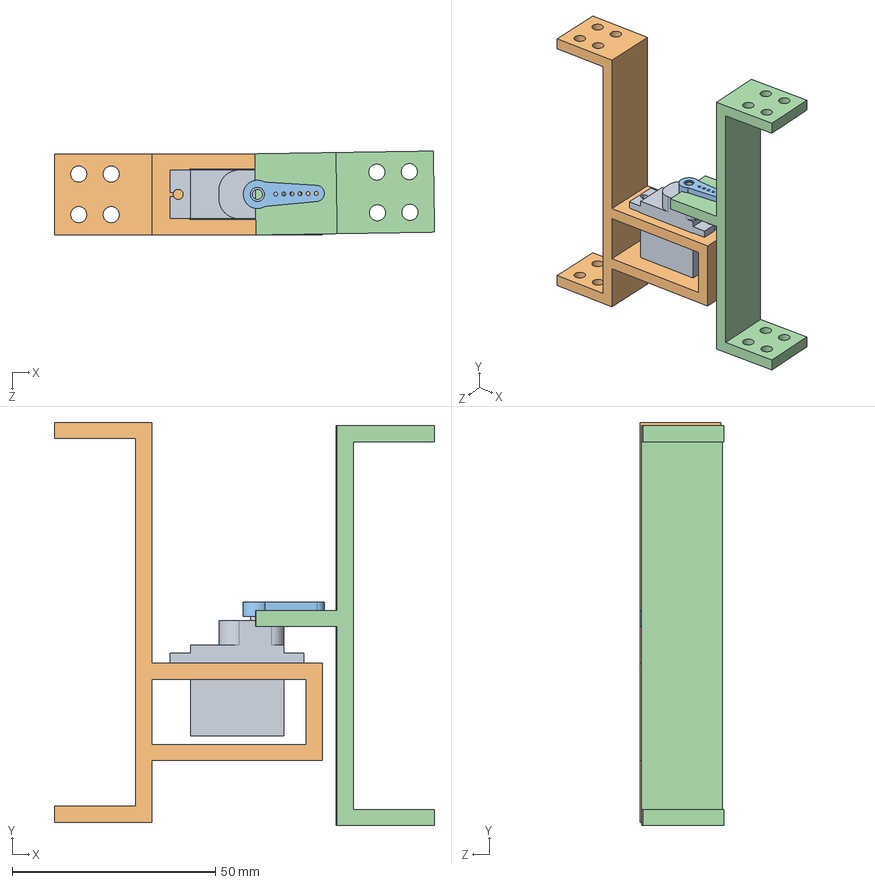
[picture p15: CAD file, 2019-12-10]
Solidworks/vertical motor alignment/skeletal/pl_proto/pl_proto_assem.SLDASM
93.7 x 99.2 x 20.7 mm
9g servo_p
m_clamp
single head_p
h_clamp

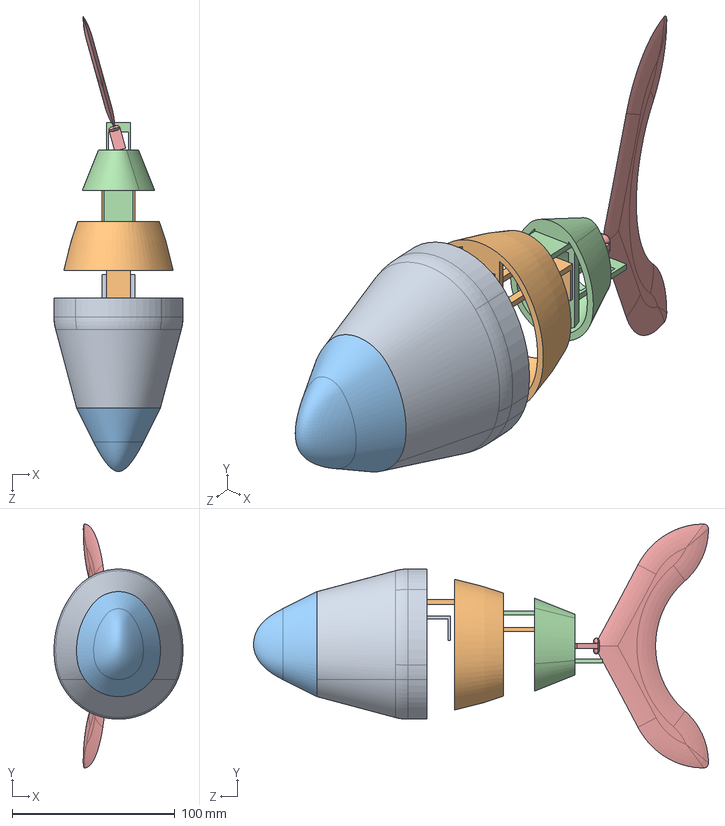
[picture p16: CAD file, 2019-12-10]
Solidworks/vertical motor alignment/skeletal/skeletal_cmc/small motor_cmc/Subcarangiform_2_vs.SLDASM
79.3 x 150.0 x 279.7 mm
Head_1_3_vs
midbody_1_1_vs
nose_1s
tailbody_1_1_vs
tail_1_1vs

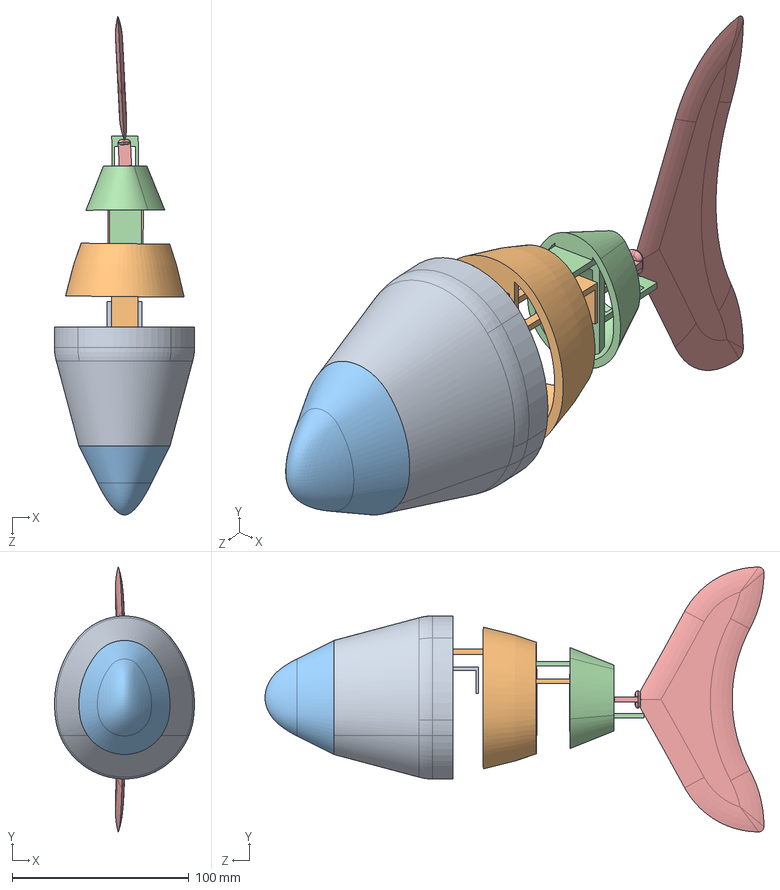
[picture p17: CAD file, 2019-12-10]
Solidworks/vertical motor alignment/small motor/SM with gasket/Subcarangiform_2_vsg.SLDASM
79.3 x 150.0 x 282.6 mm
Head_1_3_vsg
midbody_1_1_vsg
nose_1sg
tailbody_1_1_vsg
tail_1_1vsg

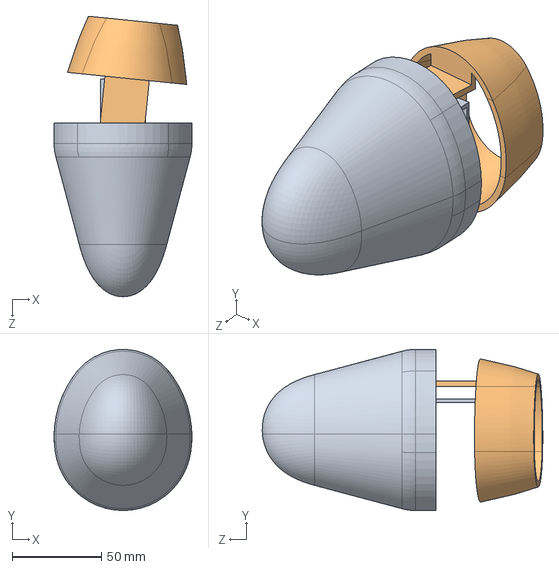
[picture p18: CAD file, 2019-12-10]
Solidworks/vertical motor alignment/skeletal/skeletal_c_m/Subcarangiform_1_v_scm.SLDASM
77.3 x 90.2 x 157.3 mm
Head_1_2_v
midbody_1_1_v

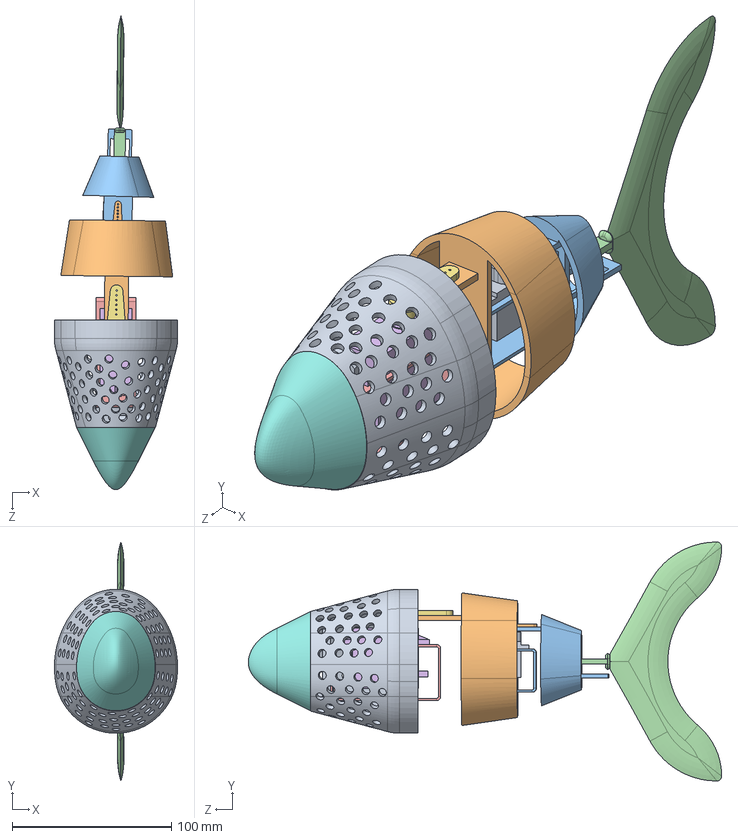
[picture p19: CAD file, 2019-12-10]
Solidworks/vertical motor alignment/skeletal/skeletal_c_m/Subcarangiform_2_v_scm.SLDASM
77.3 x 150.0 x 297.1 mm
Head_1_3_v_scm
midbody_1_1_v_scm
tailbody_1_1_v_scm
tail_1_1v_scm
clamp_1sm
15kgcm servo_scm
single side header_scm
nose_1_scm
9g servo_scm
single head_scm
clamp_1mm

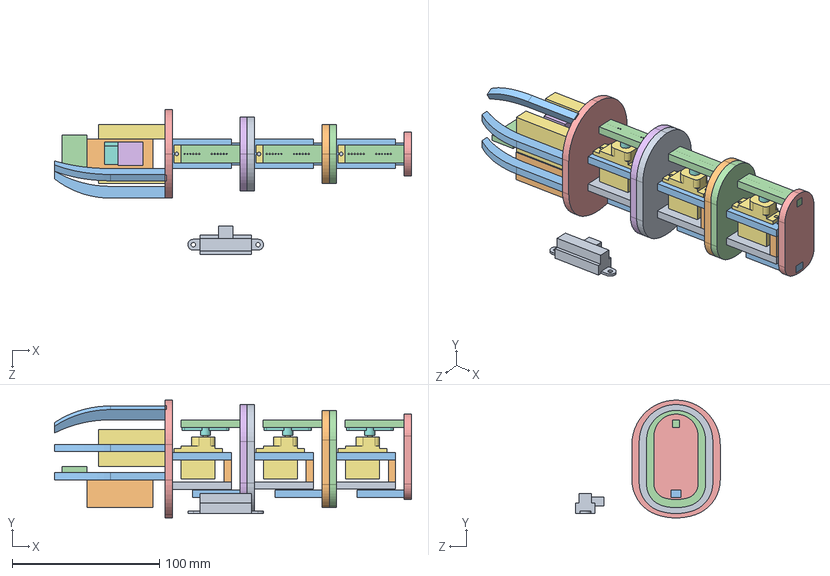
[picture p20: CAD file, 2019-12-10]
Solidworks/vertical motor alignment/skeletal/skeletal_cmc/chain subassem_a/chain assembly_a.SLDASM
242.2 x 80.0 x 98.1 mm
ch_h_l x 3
ch_h_m x 3
ch_h_u x 3
ch_t_u x 3
chain head_cmc_a
chain tail_j1_cmc_a
9g servo_cmc x 3
dual header_cmc x 3
chain head_j1_cmc_a
chain tail_j2_cmc_a
ch_t_l x 3
chain head_j2_cmc_a
chain tail_cmc_a
buck_cnvrtr
lipo x 2
MPU6050
sharp_sensor
arduino_nano
s1 x 3
lipo_charger_ckt

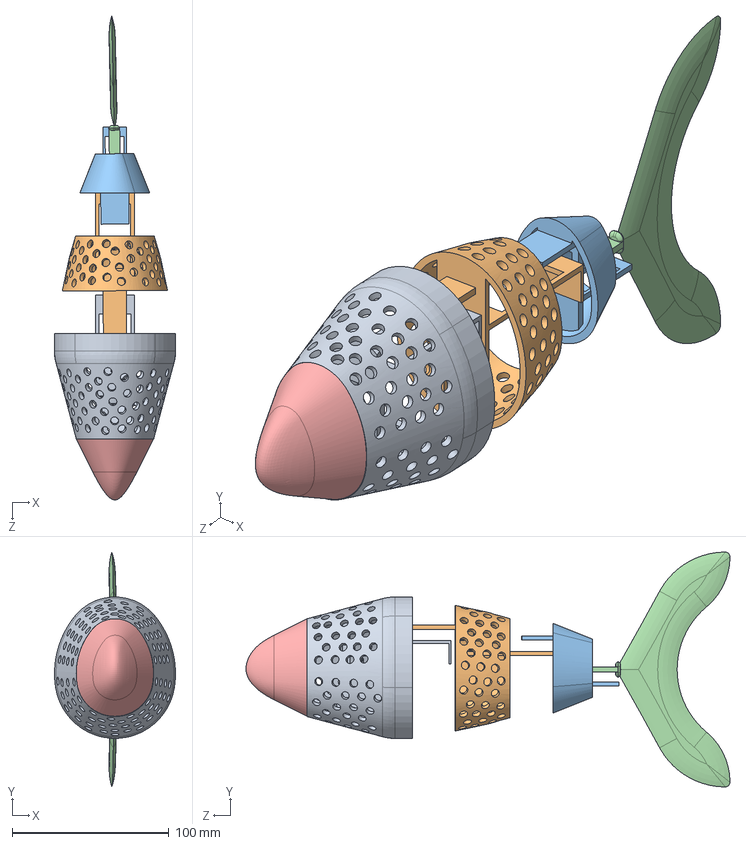
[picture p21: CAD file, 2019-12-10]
Solidworks/vertical motor alignment/skeletal/sSubcarangiform_2_v.SLDASM
77.3 x 150.0 x 309.1 mm
sHead_1_3_v
smidbody_1_1_v
stailbody_1_1_v
stail_1_1v
snose_1

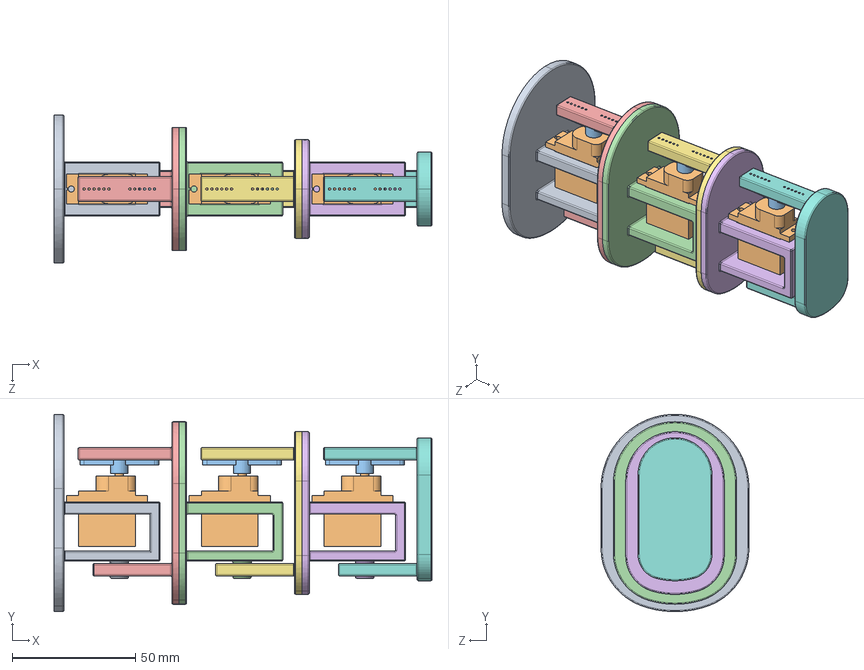
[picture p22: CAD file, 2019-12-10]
Solidworks/vertical motor alignment/skeletal/skeletal_cmc/chain subassem/Chain subassem_2.SLDASM
153.2 x 80.0 x 60.0 mm
chain head_cmc
9g servo_cmc x 3
dual header_cmc x 3
chain head_j1_cmc
chain tail_j1_cmc
chain head_j2_cmc
chain tail_j2_cmc
chain tail_cmc

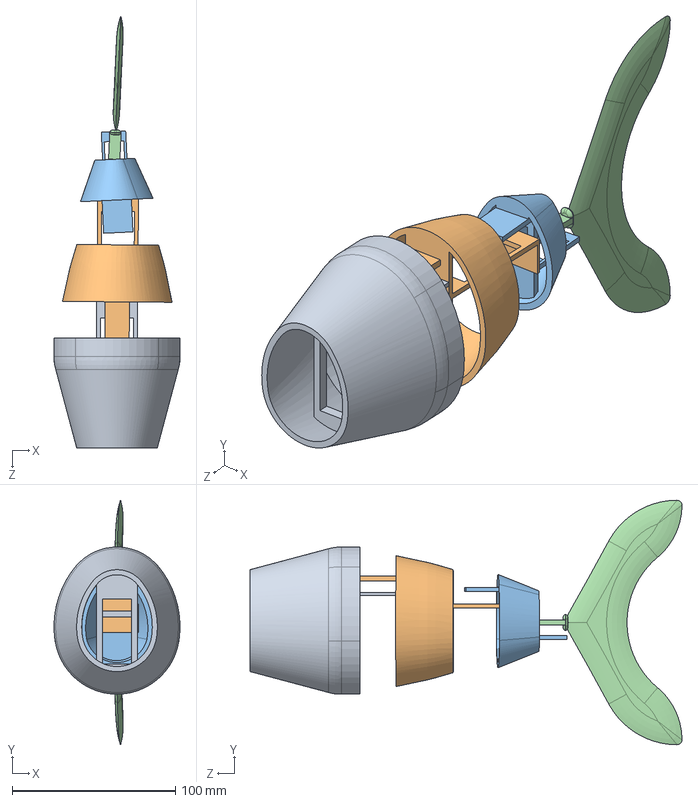
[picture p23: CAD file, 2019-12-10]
Solidworks/vertical motor alignment/Subcarangiform_2_v.SLDASM
77.3 x 150.0 x 265.0 mm
Head_1_3_v
midbody_1_1_v
tailbody_1_1_v
tail_1_1v

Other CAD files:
Solidworks/Horizontal motor alignment/Head_1_3_hs.SLDPRT
Solidworks/Horizontal motor alignment/midbody_1_1_hs.SLDPRT
Solidworks/Horizontal motor alignment/nose_1hs.SLDPRT
Solidworks/Horizontal motor alignment/tail_1_1_hs.SLDPRT
Solidworks/Horizontal motor alignment/tailbody_1_1_hs.SLDPRT
Solidworks/bellow grabcad.SLDPRT
Solidworks/bellow__.SLDPRT
Solidworks/vertical motor alignment/15 kgcm servo/15kgcm servo.SLDPRT
Solidworks/vertical motor alignment/15 kgcm servo/large duo coupling.SLDPRT
Solidworks/vertical motor alignment/15 kgcm servo/round coupling.SLDPRT
Solidworks/vertical motor alignment/15 kgcm servo/single side header.SLDPRT
Solidworks/vertical motor alignment/15 kgcm servo/small duo coupling.SLDPRT
Solidworks/vertical motor alignment/Head_1_1_v.SLDPRT
Solidworks/vertical motor alignment/Head_1_2_v.SLDPRT
Solidworks/vertical motor alignment/Head_1_3_v.SLDPRT
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

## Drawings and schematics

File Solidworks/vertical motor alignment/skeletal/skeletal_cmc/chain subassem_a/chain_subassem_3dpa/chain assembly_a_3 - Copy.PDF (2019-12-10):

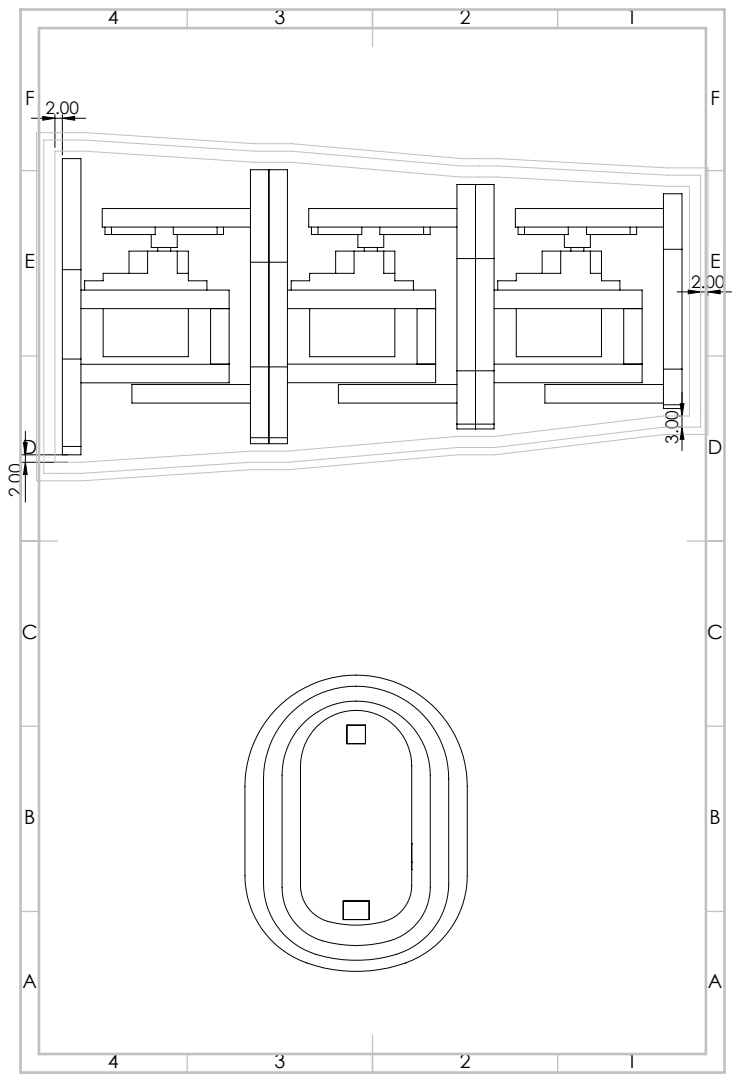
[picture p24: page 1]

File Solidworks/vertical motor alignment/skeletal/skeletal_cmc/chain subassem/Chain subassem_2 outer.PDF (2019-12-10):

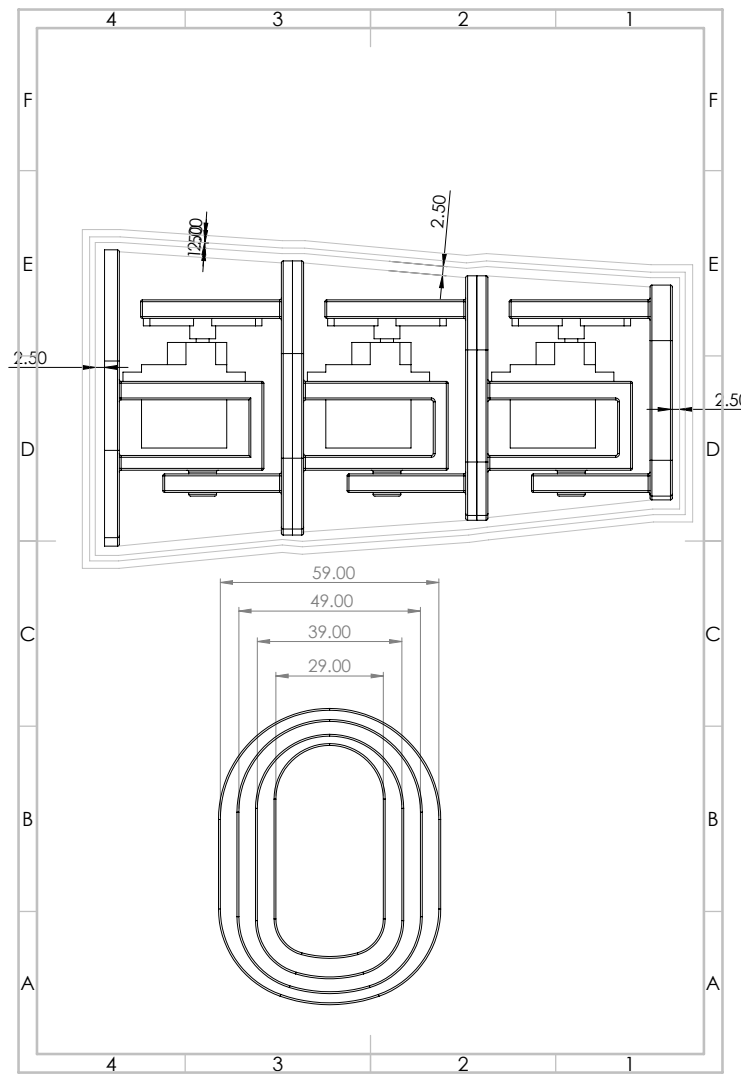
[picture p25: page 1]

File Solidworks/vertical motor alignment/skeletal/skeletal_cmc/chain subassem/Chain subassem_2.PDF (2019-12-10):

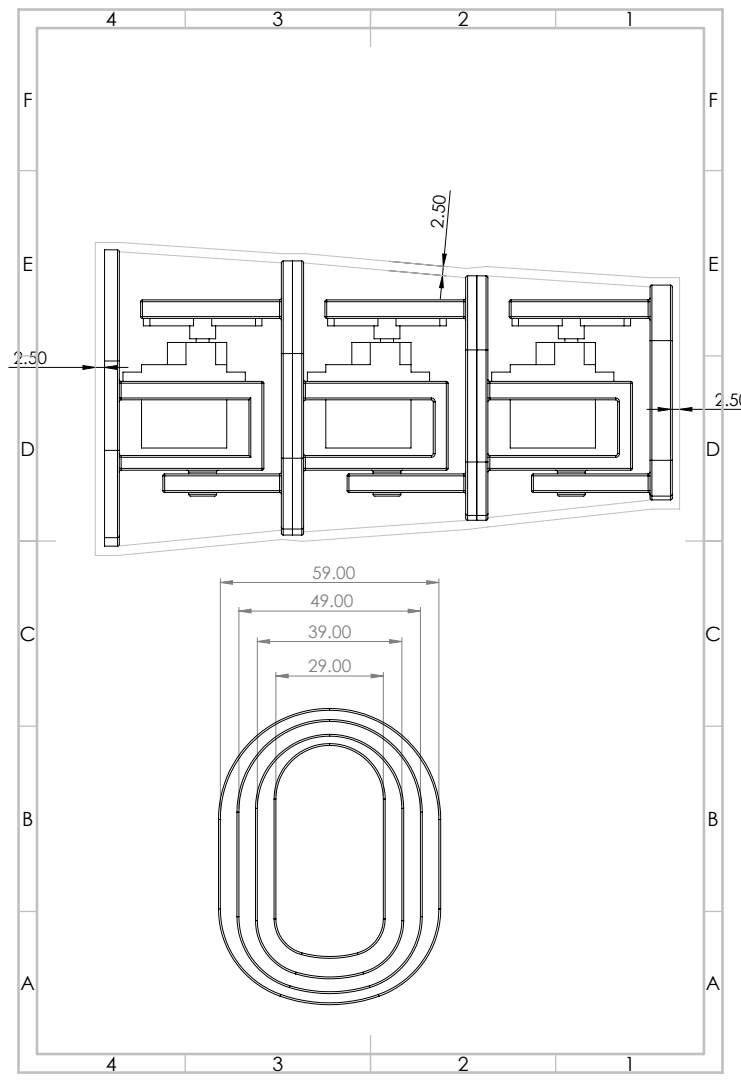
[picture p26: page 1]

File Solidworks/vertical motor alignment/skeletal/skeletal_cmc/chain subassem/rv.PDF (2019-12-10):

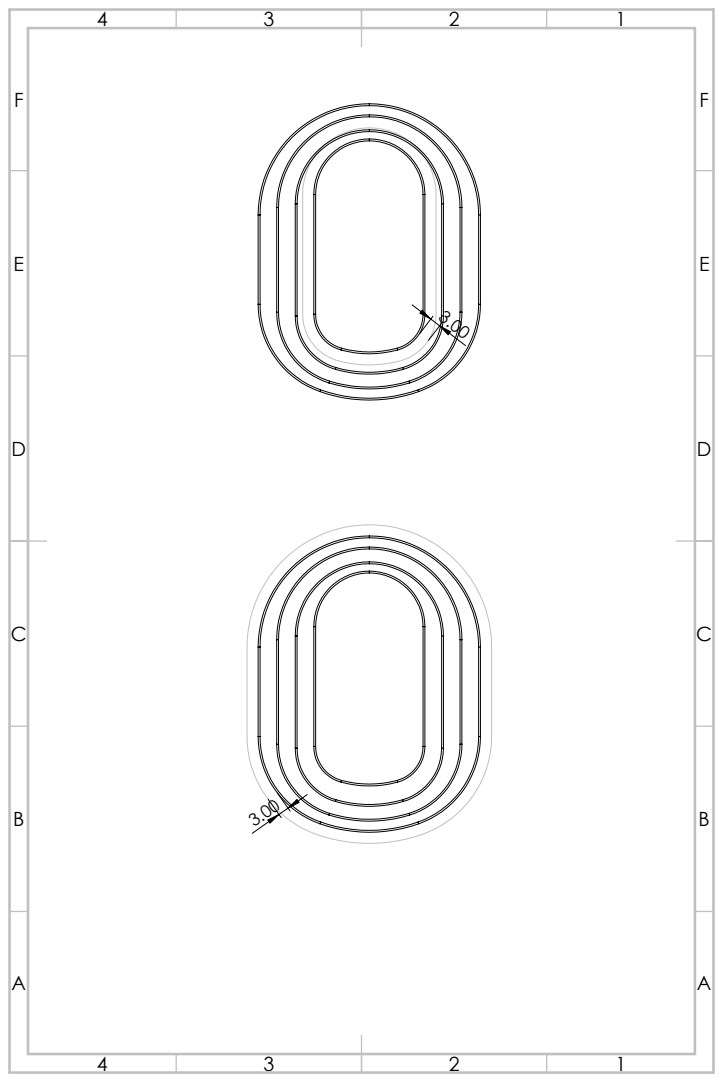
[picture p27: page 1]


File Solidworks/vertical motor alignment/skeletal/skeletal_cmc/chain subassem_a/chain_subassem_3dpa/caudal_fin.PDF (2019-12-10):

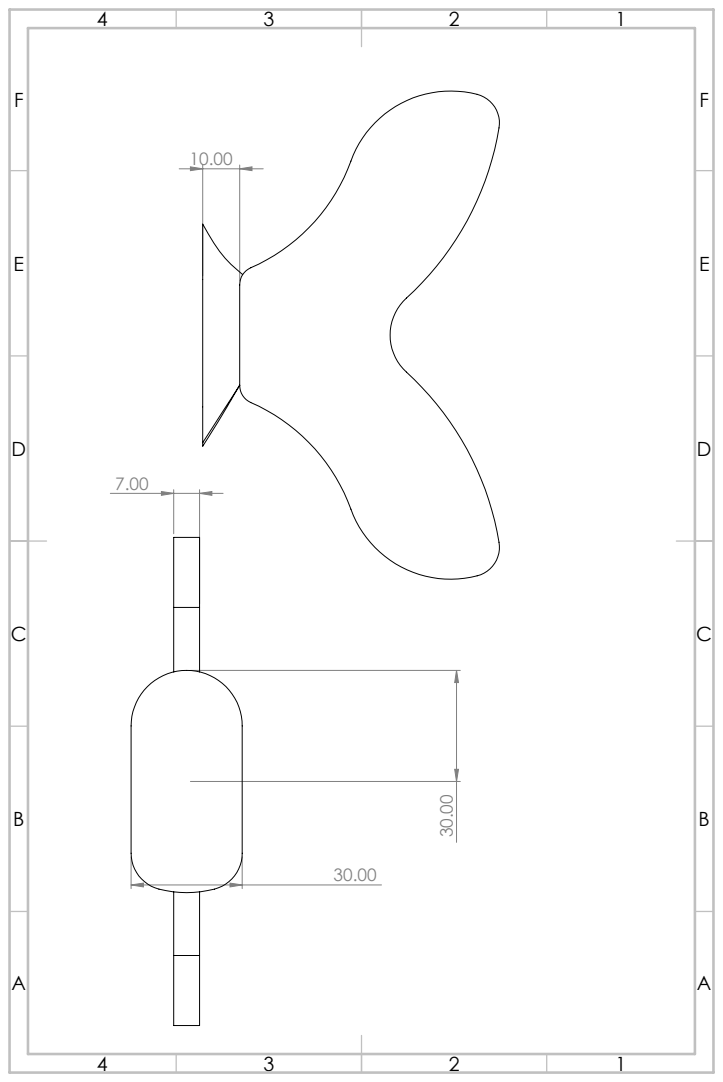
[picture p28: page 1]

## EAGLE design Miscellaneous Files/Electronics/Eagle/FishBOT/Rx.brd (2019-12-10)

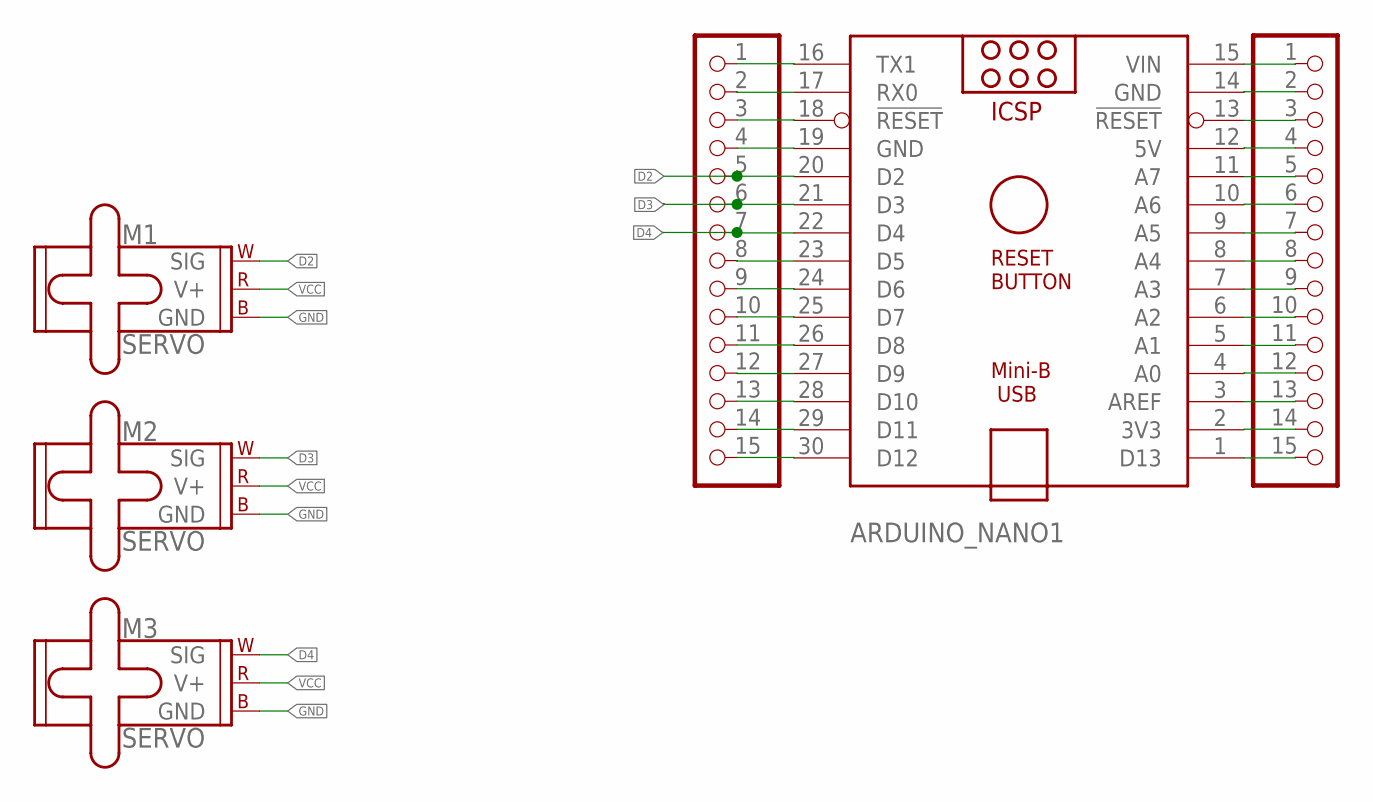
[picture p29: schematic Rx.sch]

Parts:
ARDUINO_NANO1: ARDUINO_NANO
JP1, JP2: PINHD-1X15-CB; 1X15-CB
M1, M2, M3: SERVO; 1X03

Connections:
D2: ARDUINO_NANO1.20 (D2), JP2.5, M1.1 (SIG)
D3: ARDUINO_NANO1.21 (D3), JP2.6, M2.1 (SIG)
D4: ARDUINO_NANO1.22 (D4), JP2.7, M3.1 (SIG)
GND: M1.3 (GND), M2.3 (GND), M3.3 (GND)
unnamed: ARDUINO_NANO1.16 (TX1), JP2.1
unnamed: ARDUINO_NANO1.17 (RX0), JP2.2
unnamed: ARDUINO_NANO1.18 (!RESET), JP2.3
unnamed: ARDUINO_NANO1.19 (GND), JP2.4
unnamed: ARDUINO_NANO1.23 (D5), JP2.8
unnamed: ARDUINO_NANO1.24 (D6), JP2.9
unnamed: ARDUINO_NANO1.25 (D7), JP2.10
unnamed: ARDUINO_NANO1.26 (D8), JP2.11
unnamed: ARDUINO_NANO1.27 (D9), JP2.12
unnamed: ARDUINO_NANO1.28 (D10), JP2.13
unnamed: ARDUINO_NANO1.29 (D11), JP2.14
unnamed: ARDUINO_NANO1.30 (D12), JP2.15
unnamed: ARDUINO_NANO1.15 (VIN), JP1.1
unnamed: ARDUINO_NANO1.14 (GND), JP1.2
unnamed: ARDUINO_NANO1.13 (!RESET), JP1.3
unnamed: ARDUINO_NANO1.12 (5V), JP1.4
unnamed: ARDUINO_NANO1.11 (A7), JP1.5
unnamed: ARDUINO_NANO1.10 (A6), JP1.6
unnamed: ARDUINO_NANO1.9 (A5), JP1.7
unnamed: ARDUINO_NANO1.8 (A4), JP1.8
unnamed: ARDUINO_NANO1.7 (A3), JP1.9
unnamed: ARDUINO_NANO1.6 (A2), JP1.10
unnamed: ARDUINO_NANO1.5 (A1), JP1.11
unnamed: ARDUINO_NANO1.4 (A0), JP1.12
unnamed: ARDUINO_NANO1.3 (AREF), JP1.13
unnamed: ARDUINO_NANO1.2 (3V3), JP1.14
unnamed: ARDUINO_NANO1.1 (D13), JP1.15
VCC: M1.2 (V+), M2.2 (V+), M3.2 (V+)

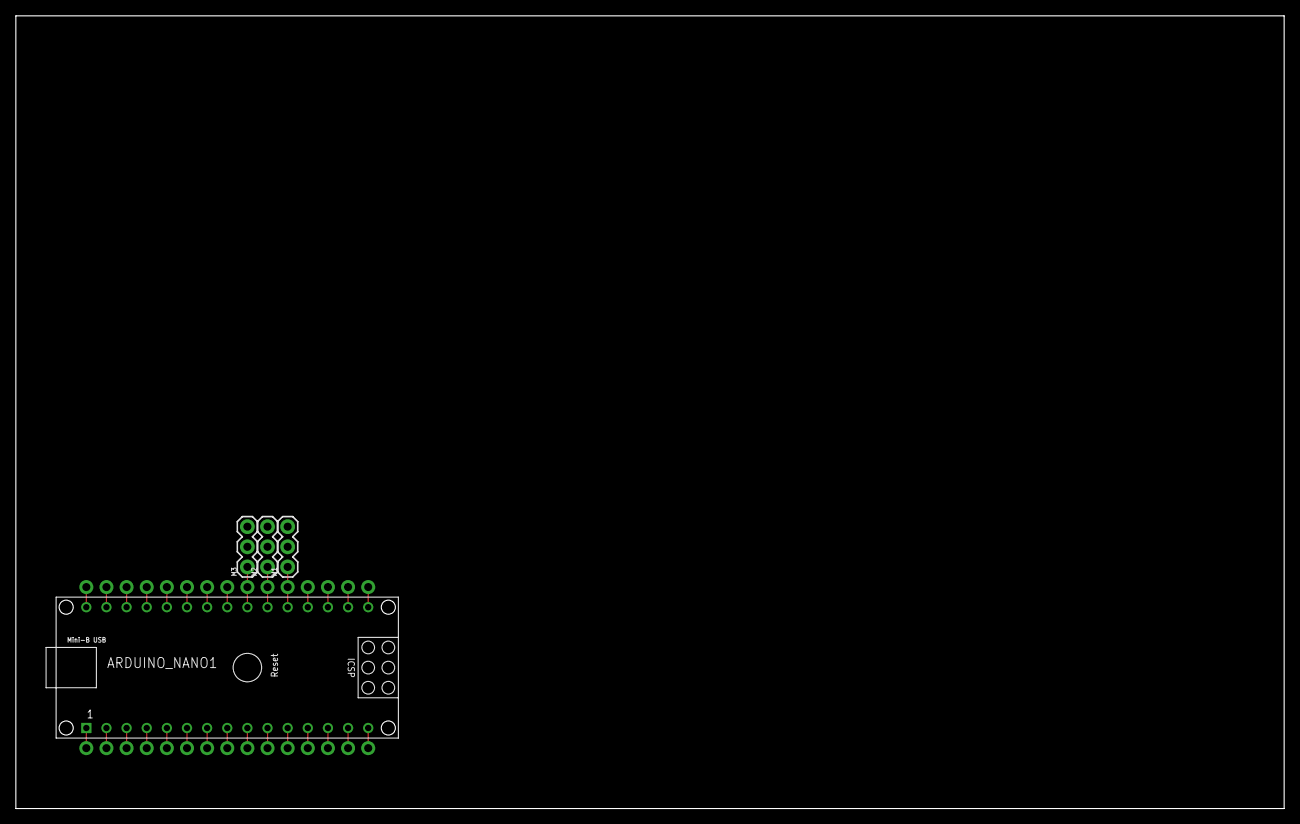
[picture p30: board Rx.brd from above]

Board: 2 copper layers, 160.0 x 100.0 mm, 6 parts (1 on the bottom side), 32 nets.

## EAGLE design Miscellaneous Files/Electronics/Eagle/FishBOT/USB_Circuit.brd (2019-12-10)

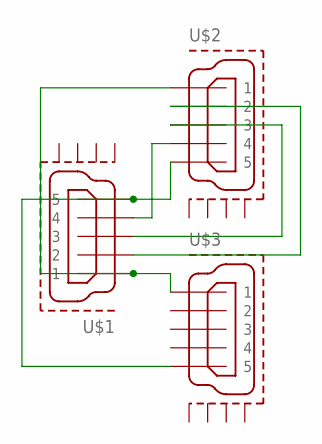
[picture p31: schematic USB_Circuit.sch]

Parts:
U$1, U$2, U$3: MICRO-USB-RECEPTACLE47589-0001; 47589-0001

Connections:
unnamed: U$1.5, U$2.5, U$3.5
unnamed: U$1.3, U$2.3
unnamed: U$1.2, U$2.2
unnamed: U$1.4, U$2.4
unnamed: U$1.1, U$2.1, U$3.1

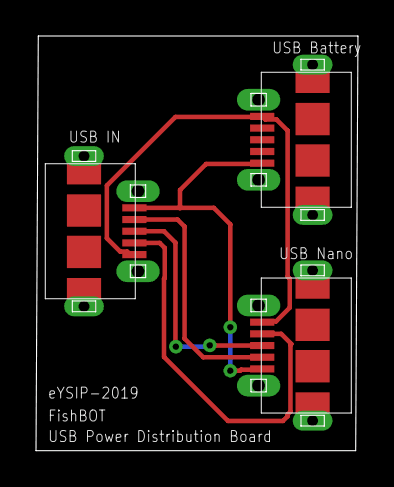
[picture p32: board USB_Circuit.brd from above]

Board: 2 copper layers, 17.9 x 23.0 mm, 3 parts (0 on the bottom side), 5 nets.

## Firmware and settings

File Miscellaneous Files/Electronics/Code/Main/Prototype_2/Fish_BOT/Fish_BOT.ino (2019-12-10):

/*
  ▪ Project Name: Bio-Inspired Sub-Carangiform FishBOT
  ▪ Team Name: Aditya Kumar Singh, Bhavy Shah
  ▪ Author List: Aditya Kumar Singh
  ▪ Filename: Fish_BOT.ino
  ▪ Functions: motd(), start_radio_communication(), get_Data(), updateReplyData(), get_controller_data(), execute_motion(),
               Timer_init(), setup(), loop()
  ▪ Global Variables: timer_counter, listen, thisSlaveAddress[5], dataReceived[3], ackData[2],counter, frequency, a, b, c, num_segments,
                      gamma, beta, amplitude, offset_0, offset_1, offset_2, delayTimeovements, startPause, connected
*/

/*
   Including necessary library files.
*/
#include <SPI.h>
#include <nRF24L01.h>
#include <RF24.h>
#include <Servo.h>

#define pi 3.14159

#define CE_PIN   9
#define CSN_PIN 10

volatile int timer_counter=0;                                            //Variable to count then number of times TIMER2_COMPA occurs.
bool listen = false;                                                     //Flag variable to make the BOT listen to remote signals

/*
  ▪ Function Name: ISR(TIMER2_COMPA_vect)
  ▪ Input: None
  ▪ Output: None
  ▪ Logic: This interrupt routine is called whenever Timer 2 counter matches OCR2A. Listen variable makes the BOT to listen to signal.
           So, for every 3 times matches occur, the BOT will isten to signal and then process it.
  ▪ Example Call: Called automatically.
*/
ISR(TIMER2_COMPA_vect) {
  timer_counter++;              
  if(timer_counter>=3){
    listen = true;
    timer_counter=0;                                                     //Reset back to 0
  }
}

/*
 Creating servo objects 
*/ 
Servo s1;                                                               //Handles mid body servo
Servo s2;                                                               //Handles posteriror body servo
Servo s3;                                                               //Handles caudal fin servo

RF24 radio(CE_PIN, CSN_PIN);                                            //Creating radio object to handle radio comuunication using NRF24L01

const byte thisSlaveAddress[5] = {'P', 'I', 'S', 'Y', 'e'};             //Slave address in which the BOT will listen.

char dataReceived[3];                                                   //Variable to store the data which will come from Transmitter.
int ackData[2] = {100, 100};                                            //Data which will be acknowledged back once a data is received.

/*
  SERPENTINE MOTION 
*/
int counter = 0;                                                        // Loop counter variable (will go from 0 to 360)
int frequency = 3 ;                                                     // Variable to control freqeuncy of the oscilation of the joints
float a = 50;                                                           //Amplitude coeffecient of the motion
float b = 1 * pi;                                                       //Curve Coeffecient of the motion
float c = 0;                                                            //Turn Coeffecient of the motion
int num_segments = 3;                                                   //Number of joints (in our BOT its 3)

float gamma = -c / num_segments;                                        //Turn according to turn coeffecient
float beta = b / num_segments;                                          //Curve ccording to Curve coeffecient.
float amplitude = a * abs(sin(beta / 2));                               //Amplitude of the motion using Amplitude coeffecient.

/*
  Offset angles for respective servo joint
 */
float offset_0 = -5;                                                    
float offset_1 = 10; 
float offset_2 = -3;

int delayTime = 5;                                                     // Delay between limb movements
int startPause = 100;                                                  // Delay time to position robot once the robot is powered

bool connected = 0;                                                    //Flag variable to check the connectivity status

/*
  ▪ Function Name: motd
  ▪ Input: None
  ▪ Output: None
  ▪ Logic: This function just prints the message of the day on the Serial line.
  ▪ Example Call: motd()
*/
void motd() {
  Serial.println("Intialising........");
  delay(100);
  Serial.println("====================================================");
  delay(50);
  Serial.println("      ______ _     _     ____   ____ _______ ");
  delay(50);
  Serial.println("     |  ____(_)   | |   |  _ \\ / __ \\__   __|");
  delay(50);
  Serial.println("     | |__   _ ___| |__ | |_) | |  | | | |  ");
  delay(50);
  Serial.println("     |  __| | / __| \'_ \\|  _ <| |  | | | | ");
  delay(50);
  Serial.println("     | |    | \\__ \\ | | | |_) | |__| | | |  ");
  delay(50);
  Serial.println("     |_|    |_|___/_| |_|____/ \\____/  |_| ");
  delay(50);
  Serial.println("");
  delay(50);
  Serial.println("====================================================");
}

/*
  ▪ Function Name: start_radio_communication
  ▪ Input: None
  ▪ Output: None
  ▪ Logic: This function configures the NRF24L01 and starts the communication in Reciever mode.
  ▪ Example Call: start_radio_communication() 
*/
void start_radio_communication() {
  Serial.println("\nIntialsing Radio Module....");
  radio.begin();                                          //Initiallising the module
  radio.setChannel(127);                                  //Channel frequency to 
  radio.setDataRate( RF24_250KBPS );                      //Data rate to 250Kbps
  radio.openReadingPipe(1, thisSlaveAddress);             //Open pipe number 1 to read the data.
  radio.enableAckPayload();                               //Enabling auto acknowledge mode.
  radio.startListening();                                 //Puts the NRF to receiver mode
  radio.writeAckPayload(1, &ackData, sizeof(ackData));    // pre-load data
  Serial.println("DONE.\n");
}

/*
  ▪ Function Name: getData
  ▪ Input: None
  ▪ Output: None
  ▪ Logic: This function reads the data from NRF(if available) and store it. After that,
           it acknowledges back the transmitter with some data.
  ▪ Example Call: getData()
*/
void getData() {
  if ( radio.available() ) {
    radio.read( &dataReceived, sizeof(dataReceived) );
    if (connected) {                                                //If already connected
      if (dataReceived[0] == 'f' && dataReceived[1] == 'b') {       //But data recieved is that of attmepting to connect
        /*
            So, in this case it agains tries to connect.
        */
        ackData[0] = 100;
        ackData[1] = 100;
        connected = 0;                                              //Resetting the connection
        Serial.println("\n================================");
        Serial.println("    CONNECTION LOST.");
        Serial.println("================================\n");
        Serial.println("Re-connecting....");
      }
    }
    else {                                                          //If not connected
      if (dataReceived[0] == 'f' && dataReceived[1] == 'b') {       //Data recevived is for attempting to connect
        connected = 1;                                              //Connection succesfull
        Serial.println("\n================================");
        Serial.println("    Succesfully connected.");
        Serial.println("================================\n");
        ackData[0] = 101;                                           //Change acknowledged message
        ackData[1] = 101;
      }
      else {
        Serial.println("Searching for Transmitter..");
      }
    }
    updateReplyData();                                               //Put the Tx message to Tx buffer.
  }
}

/*
  ▪ Function Name: updateReplyData
  ▪ Input: None
  ▪ Output: None
  ▪ Logic: This function puts the acknowledge data into Tx buffer. This is to be done after every time
           reading is complete, since afte once data is acknowledged, buffer will be empty.
  ▪ Example Call: updateReplyData()
*/
void updateReplyData() {
  radio.writeAckPayload(1, &ackData, sizeof(ackData)); // load the payload for the next time
}

/*
  ▪ Function Name: execute_motion
  ▪ Input: None
  ▪ Output: None
  ▪ Logic: This function executes the motion according to the data received.
  ▪ Example Call: execute_motion() 
*/
void  execute_motion() {
  int val;                                              //To store the speed for the data
  if (dataReceived[0] != 'X' && connected) {
    val=int(dataReceived[1])-48;                       //Get the actual number(0-4)
    frequency = 1 + 0.8*val;                        //Update the freqeuncy
    if (dataReceived[0] == 'F') {                       //Forward
      switch(val){                                      //According  the spped, amplitude and Curve have to adjusted.
        case 0 : a = 50;
                 //b = 1.1* pi;
                 c=0;
                 break;
        case 1 : a = 55;
                 //b = 1.2* pi;
                 break;
        case 2 : a = 60;
                 //b = 1.5* pi;
                  c=0;
                 break;
        case 3 : a = 65;
                 //b = 1.7* pi;
                 break;
        case 4 : a = 70;
                 //b = 2* pi;
                  c=0;
                 break;          
      }
      //Updating the coeffecients
      gamma = -c / num_segments;                                        
      beta = b / num_segments;                                          
      amplitude = a * abs(sin(beta / 2));
      //Writing the angles to servo motors
      s1.write(90 + offset_0 + amplitude * sin(frequency * counter * pi / 180 + 0 * beta) + gamma);
      s2.write(90 + offset_1 + amplitude * sin(frequency * counter * pi / 180 + 1 * beta + pi / 2) + gamma);
      s3.write(90 + offset_2 + amplitude * sin(frequency * counter * pi / 180 + 2 * beta) + gamma);
    }
    else if (dataReceived[0] == 'L') {                 //Left        
      a = 60;
      b=1*pi;
      c=20*pi;
      //Updating the coeffecients
      gamma = -c / num_segments;                                        
      beta = b / num_segments;                                          
      amplitude = a * abs(sin(beta / 2));
      //Writing the angles to servo motors
      s1.write(60);
      s2.write(90 + offset_1 + amplitude * sin(frequency * counter * pi / 180 + 1 * beta + pi / 2) + gamma);
      s3.write(90 + offset_2 + amplitude * sin(frequency * counter * pi / 180 + 2 * beta) + gamma);
    }
    else if (dataReceived[0] == 'R') {                 //Right   
      a = 60;
      b=1*pi;
      c=-20*pi;
      //Updating the coeffecients
      gamma = -c / num_segments;                                        
      beta = b / num_segments;                                          
      amplitude = a * abs(sin(beta / 2));
      //Writing the angles to servo motors
      s1.write(120);
      s2.write(90 + offset_1 + amplitude * sin(frequency * counter * pi / 180 + 1 * beta + pi / 2) + gamma);
      s3.write(90 + offset_2 + amplitude * sin(frequency * counter * pi / 180 + 2 * beta) + gamma);
    }
    else if (dataReceived[0] == 'B') {                 //Left
      frequency = 3;          
      a = 50;
      b=1*pi;
      c=0;
      //Updating the coeffecients
      gamma = -c / num_segments;                                        
      beta = b / num_segments;                                          
      amplitude = a * abs(sin(beta / 2));
      //Writing the angles to servo motors
      s3.write(90 + offset_0 + amplitude * sin(frequency * counter * pi / 180 + 0 * beta) + gamma);
      s2.write(90 + offset_1 + amplitude * sin(frequency * counter * pi / 180 + 1 * beta + pi / 2) + gamma);
      s1.write(90 + offset_2 + amplitude * sin(frequency * counter * pi / 180 + 2 * beta) + gamma);
    }
      delay(delayTime);                                //Wait for some time to let servo go to their setted position.
      counter++;                           
      if(counter>360){                                 //If counter goes above 360, reset it to 0
      counter=0;
      }
  }
}

/*
  ▪ Function Name: Timer_init
  ▪ Input: None
  ▪ Output: None
  ▪ Logic: This function initallises timer 2 and sets the delay after which the BOT will listen to commands.
  ▪ Example Call: Timer_init()
*/
void Timer_init() {
  //Resetting registers
  TCCR2A = 0;                                           
  TCCR2B = 0;
  TCNT2  = 0;
  OCR2A = 255;                                          //Compare at OVF
  TCCR2A |= (1 << WGM21);                               //CTC mode   
  TCCR2B |= (1 << CS22) | (1 << CS21) | (1 << CS20);    //1024 prescaling  
  TIMSK2 |= (1 << OCIE2A);                              //Interrupt at compare match
}

/*
  ▪ Function Name: setup
  ▪ Input: None
  ▪ Output: None
  ▪ Logic: This function setups the whole harwadre and starte the Serial communication. 
           This is automatically called from main().
  ▪ Example Call: setup()
*/
void setup() {
  Serial.begin(9600);                                   //Starting Serial communication
  cli();                                                //Clear interrupts
  motd();                                               //Display message of the day
  Timer_init();                                         //Initiallising timer 2
  start_radio_communication();                          //Configure NRF24L01 for communication.
  //Attaching servos
  s1.attach(2);
  s2.attach(3);
  s3.attach(4);
  //Bringing all se4rvos to 90 deg initially.
  s1.write(90 + offset_0);
  s2.write(90 + offset_1);
  s3.write(90 + offset_2);
  sei();                                                //Interrupts enabled
  delay(startPause);                                    //Holds the progrma for small time.
}

/*
  ▪ Function Name: loop
  ▪ Input: None
  ▪ Output: None
  ▪ Logic: This function is automatically called from while(1) loop from main(). 
           It execute the motion and gets the data once the timer 2 counts upto the setted delay. 
  ▪ Example Call: loop()
*/
void loop() {
  if(listen){                                           //If delay is over, listen to remote
    getData();                                          //Get the data
    listen= false;                                      //Reset flag again
  }
  execute_motion();                                     //Execute the motion
}

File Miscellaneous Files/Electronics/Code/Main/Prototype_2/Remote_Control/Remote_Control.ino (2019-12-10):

/*
  ▪ Project Name: Bio-Inspired Sub-Carangiform FishBOT
  ▪ Team Name: Aditya Kumar Singh, Bhavy Shah
  ▪ Author List: Aditya Kumar Singh
  ▪ Filename: Remote_Control.ino
  ▪ Functions: motd(), start_radio_communication(), controller_initialisation(), prepare_data(int, int), get_controller_data(),
               send(), setup(), loop()
  ▪ Global Variables: slaveAddress[5], dataToSend[3], ackData[2], currentMillis, prevMillis, txIntervalMillis, control_x, 
                      control_y, dir_x, dir_y, connected, led_state
*/

/*
   Including necessary library files.
*/
#include <SPI.h>
#include <nRF24L01.h>
#include <RF24.h>

#define CE_PIN   9
#define CSN_PIN 10

#define DIR_X A0
#define DIR_Y A1
#define DIR_SW 2

#define CONTROL_X A2
#define CONTROL_Y A3
#define CONTROL_SW 3

#define RED 4
#define GREEN 5
#define BLUE 6

RF24 radio(CE_PIN, CSN_PIN);                                    //Creating radio object to handle radio comuunication using NRF24L01

const byte slaveAddress[5] = {'P', 'I', 'S', 'Y', 'e'};         //Slave address to which this code will communicate.

char dataToSend[3] = "X0";                                      //Data which will be sent.
int ackData[2] = { -1, -1};                                     //Variable to store the acknowledged data. 

unsigned long currentMillis;                                    //To store the current time (in ms)
unsigned long prevMillis;                                       //History time(in ms)
unsigned long txIntervalMillis = 100;                           //Interval gap(in ms) after which message will be sent to receiver.

int control_x, control_y, dir_x, dir_y;                         //Variables to store the data from the two Joysticks.

bool connected = 0;                                             // Flag variable to check whether Transmitter found any suitable receiver or not.
bool led_state = 1;                                             // Flag variable to toggle the on board LED. 

/*
  ▪ Function Name: motd
  ▪ Input: None
  ▪ Output: None
  ▪ Logic: This function just prints the message of the day on the Serial line.
  ▪ Example Call: motd()
*/
void motd() {                                                   //Message of the Day
  Serial.println("Intialising........");
  delay(100);
  Serial.println("====================================================");
  delay(50);
  Serial.println("      ______ _     _     ____   ____ _______ ");
  delay(50);
  Serial.println("     |  ____(_)   | |   |  _ \\ / __ \\__   __|");
  delay(50);
  Serial.println("     | |__   _ ___| |__ | |_) | |  | | | |  ");
  delay(50);
  Serial.println("     |  __| | / __| \'_ \\|  _ <| |  | | | | ");
  delay(50);
  Serial.println("     | |    | \\__ \\ | | | |_) | |__| | | |  ");
  delay(50);
  Serial.println("     |_|    |_|___/_| |_|____/ \\____/  |_| ");
  delay(50);
  Serial.println("");
  delay(50);
  Serial.println("====================================================");
}


/*
  ▪ Function Name: start_radio_communication
  ▪ Input: None
  ▪ Output: None
  ▪ Logic: This function configures the NRF24L01 and starts the communication.
  ▪ Example Call: start_radio_communication() 
*/
void start_radio_communication() {
  Serial.println("\nIntialsing Radio Module....");
  radio.begin();                                    //Initiallising the module
  radio.setChannel(127);                            //Channel frequency to 
  radio.setDataRate( RF24_250KBPS );                //Data rate to 250Kbps
  radio.enableAckPayload();                         //Enabling auto acknowledge mode.
  radio.setRetries(3, 5);                           //Setting retries if Tx fails.
  radio.openWritingPipe(slaveAddress);              //Givng the slave addres to which it will communicate.
  Serial.println("DONE.\n");
}

/*
  ▪ Function Name: controller_initialisation
  ▪ Input: None
  ▪ Output: None
  ▪ Logic: This function sets the microcontroller in order the read data from the Joystick modules.
  ▪ Example Call: controller_initialisation()
*/
void controller_initialisation() {
  Serial.println("\nIntialsing Controller....");
  pinMode(CONTROL_X, INPUT);
  pinMode(CONTROL_Y, INPUT);
  pinMode(CONTROL_SW, INPUT);
  pinMode(DIR_X, INPUT);
  pinMode(DIR_Y, INPUT);
  pinMode(DIR_SW, INPUT);

  pinMode(RED, OUTPUT);
  pinMode(BLUE, OUTPUT);
  pinMode(GREEN, OUTPUT);
  digitalWrite(RED, HIGH);
  digitalWrite(BLUE, HIGH);
  digitalWrite(GREEN, HIGH);

  Serial.println("DONE.\n");
}

/*
  ▪ Function Name: prepare_data
  ▪ Input: int x -> This variable accepts the x-axis values of the Joystick 1.(Used to decide Forward/Backward)
           int y -> This variable accepts the y-axis values of the Joystick 2.(Used to decide Left/Right)
  ▪ Output: None
  ▪ Logic: This function preapres as what signal is to be send to receiver after processing the data from the Joysticks.
           There can be 4 signals for (Forward, Backward, Left, Right). In case of "Forward" the degree to which the Joystick 
           is bend, the more speed will be passed. This is controlled via the number after the main character as in 0 in 'F0'.
  ▪ Example Call: prepare_data(504, 409)
*/
void prepare_data(int x, int y) {
  char val;                                                         //Stores the maped the value from the 510 to 1024 into 0-5(0 inclusive)
  //Serial.print(x);Serial.print('\t');Serial.println(y);
  /*
    Decides the signal to be send based on the values returned from both the Joystick modules.
  */
  if (y > 500 && y < 510) {
    if (x > 500 && x < 510) {
      //Serial.println("Stable");
      dataToSend[0] = 'X';
      dataToSend[1] = '0';
    }
    else if (x >= 510) {
      //Serial.println("Forward");
      val=48+map(x,510,1024,0,5);                                  //The more Joystick is bend means more speed.
      //Serial.println(val);
      dataToSend[0] = 'F';
      dataToSend[1] = val;
    }
    else if (x <= 490) {
      //Serial.println("Backward");
      dataToSend[0] = 'B';
      dataToSend[1] = '3';
    }
  }
  else if (y >= 510) {
    //Serial.println("Right");
    val=48+map(y,510,1024,0,5);                                  //The more Joystick is bend means more speed.
    dataToSend[0] = 'R';
    dataToSend[1] = val;
  }
  else if (y <= 495) {
    //Serial.println("Left");
    val=48+map(y,495,0,0,5);                                  //The more Joystick is bend means more speed.
    dataToSend[0] = 'L';
    dataToSend[1] = val;
  }
}

/*
  ▪ Function Name: get_controller_data
  ▪ Input: None
  ▪ Output: None
  ▪ Logic: This function gets the data from the Joystick using analogRead().
  ▪ Example Call: get_controller_data()
*/
void get_controller_data() {
  dir_x = analogRead(DIR_X);              //Forward and backward motion control in Joystick 1
  control_y = analogRead(CONTROL_Y);      //Left and right control in Joystick 2
  prepare_data(dir_x, control_y);         //Process the data obtained.
}
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

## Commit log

2019-12-10 Solidworks files added
    [15kgcm servo.SLDPRT, 15kgcm servo_cmc.SLDPRT, 15kgcm servo_sc.SLDPRT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]
2019-12-10 Misc files added: :
    [Battery_Charger_Ciruit.fzz, NRF24L01.fzz, Rx.brd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]

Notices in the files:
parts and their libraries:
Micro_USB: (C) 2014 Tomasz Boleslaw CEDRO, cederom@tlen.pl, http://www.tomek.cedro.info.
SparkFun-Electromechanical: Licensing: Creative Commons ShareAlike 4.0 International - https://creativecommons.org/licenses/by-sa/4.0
